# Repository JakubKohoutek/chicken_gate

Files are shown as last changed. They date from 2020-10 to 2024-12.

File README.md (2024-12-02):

# Chicken Gate

This repository contains circuit diagram and code for low power chicken door using
ESP-8266 (ESP-12) microcontroller, DS3231 RTC module and 28BYJ-48 stepper motor.

## Description

Purpose of this project is to create a chicken door that will automatically open in the
given time in the morning and close in the given time in the evening.

Besides this automatic procedures, manual operation is also allowed using external button
to open or close gate whenever needed.

Configuration and time setting is possible via long pressing the external button - that
will start a WiFi access point with captive portal, so once user connects to the
`chicken-gate` WiFi, he is redirected to the settings page, where it is possible to
synchronize time or set a different timer for opening/closing the gate.

## Circuit Diagram

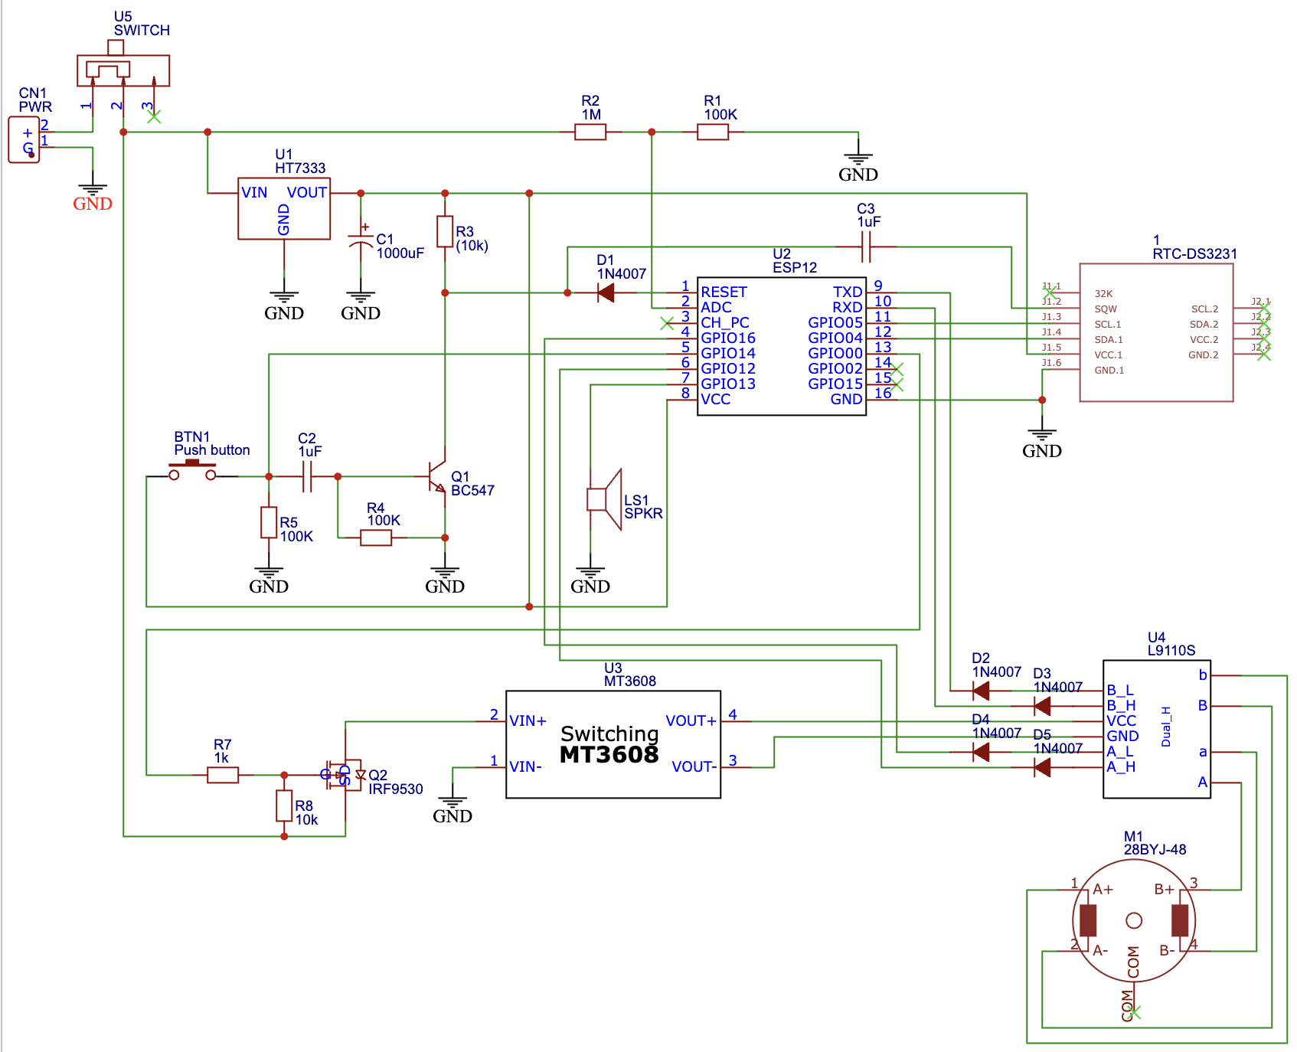
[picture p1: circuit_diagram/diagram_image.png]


## Compilation and Upload Configuration

* Board: Generic ESP8266 Module
* Upload speed: 115200
* Flash size: 4M (1M SPIFFS)

## Adjustments To Minimize Power Consumption

### RTC Module

DS3231 is a great real time clock chip, but the standard module drains too much power for
use in low power device running on battery. Fortunately it is possible to lower the power
consumption to just a few micro amps when making a few small adjustments described in
[this video](https://youtu.be/rG50U6bQhYo).

Namely, I made these adjustments:
- removed the 1k resistor to disable the power indicator LED
- bypassed the 200 ohm resistor from the "battery charging" circuit
- cut the trace from the + terminal of the battery to the VBAT pin of the chip
- added a 1N4148 diode from the + terminal of the battery to the VBAT pin of the chip
- added 1uF and 0.1uF decoupling capacitors between VBAT and GND
- lift up (or cut) the VCC pin of the DS3231 so that it doesn't connect to the board

This is how the board looks after the mods:

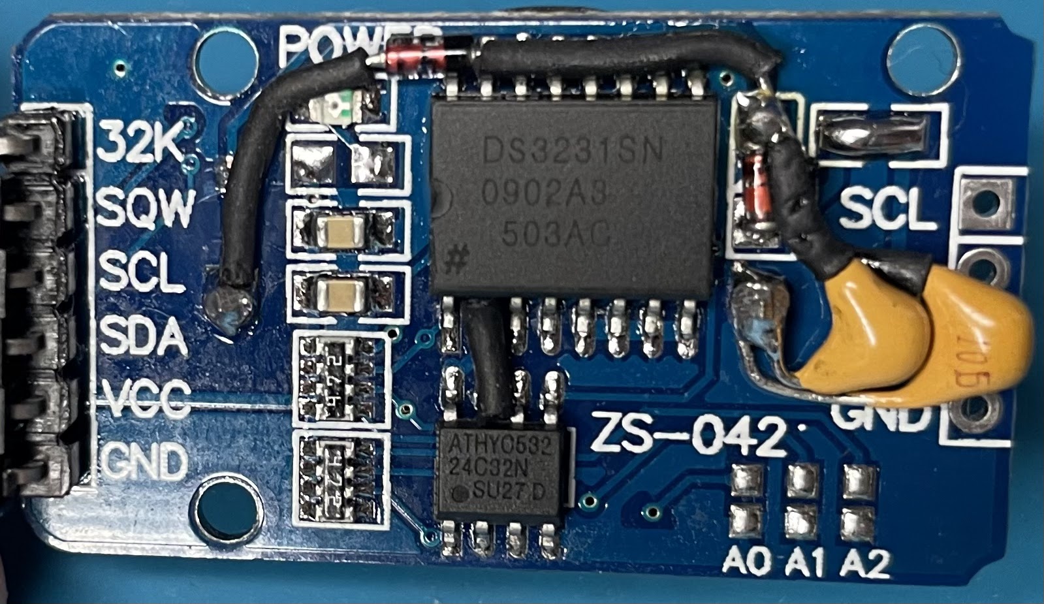
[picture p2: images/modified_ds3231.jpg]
Modified DS3231 board


Library I used to communicate with the module is available [here](https://github.com/Makuna/Rtc)

### ESP Microcontroller and Circuit

I was able to lower the power consumption of ESP-8266 board by using the deep sleep mode.
The board is woken up by an RTC module or by an external signal, so no circuit is in place
(GPIO16 connection to RST pin) for ESP to be able to wake up itself.

Current draw of the board and supplemental circuit in the deep sleep mode is about 27 uA
(~0.03 mA) and approximately 700 mA when opening/closing the gate (while stepper motor
is responsible for most of it). One operation cycle (closing, opening) takes in my case
34 seconds.

It means that in theory two operation cycles per day will drain 13.3 mAh while sleeping for
the rest of the day will drain additional 0.72 mAh. One standard day will therefore need
around 14 mAh.

It means that one 18650 battery with capacity of 1800 mAh should power the device for around
128 days, i.e. over 4 months.

## Adjustments To Improve Stepper Motor Torque

Standard 28BYJ-48 stepper motor is working in a unipolar mode. It is possible to increase
the motor torque using the bipolar mode, but it is necessary to adjust the motor in a way
described for instance in [this guide](http://www.jangeox.be/2013/10/change-unipolar-28byj-48-to-bipolar.html).

I followed these instructions and adjusted the stepper motor to increase its power to lift
up the gate.

## The Finished Product

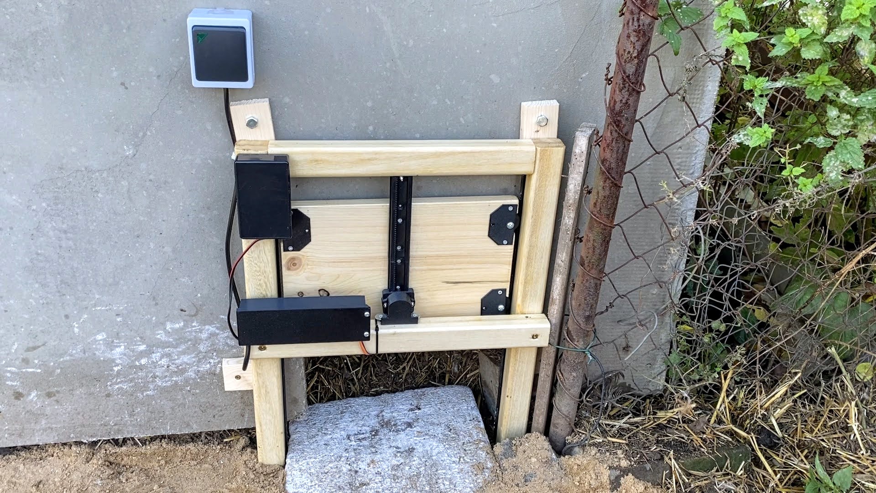
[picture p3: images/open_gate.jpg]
Open Gate

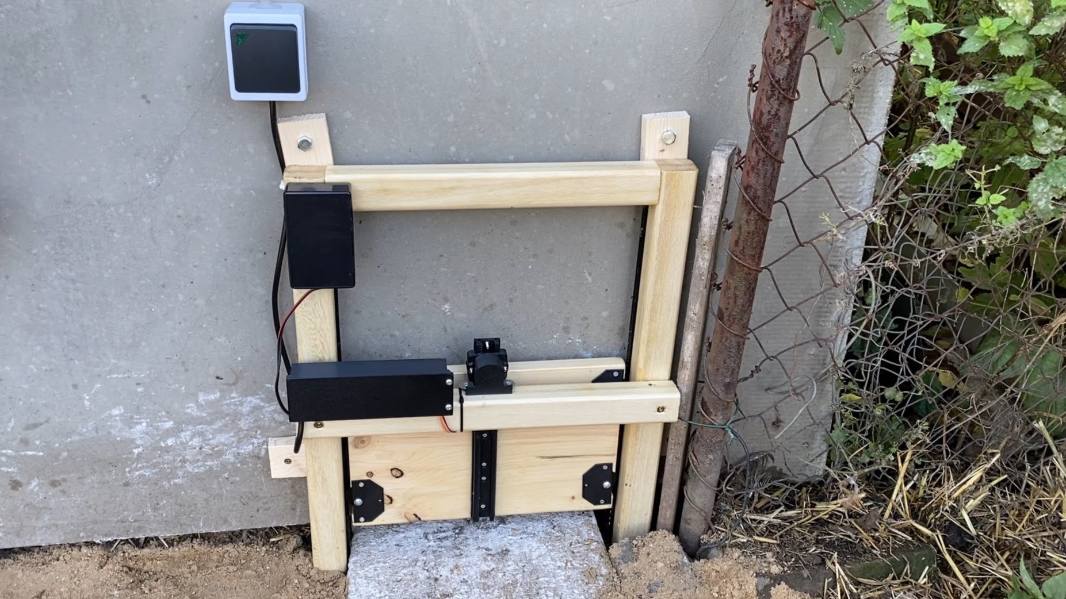
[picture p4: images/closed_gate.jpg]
Closed Gate

To see the video of working device, check out the [video on YouTube](https://youtu.be/cAucfu40Rm4).

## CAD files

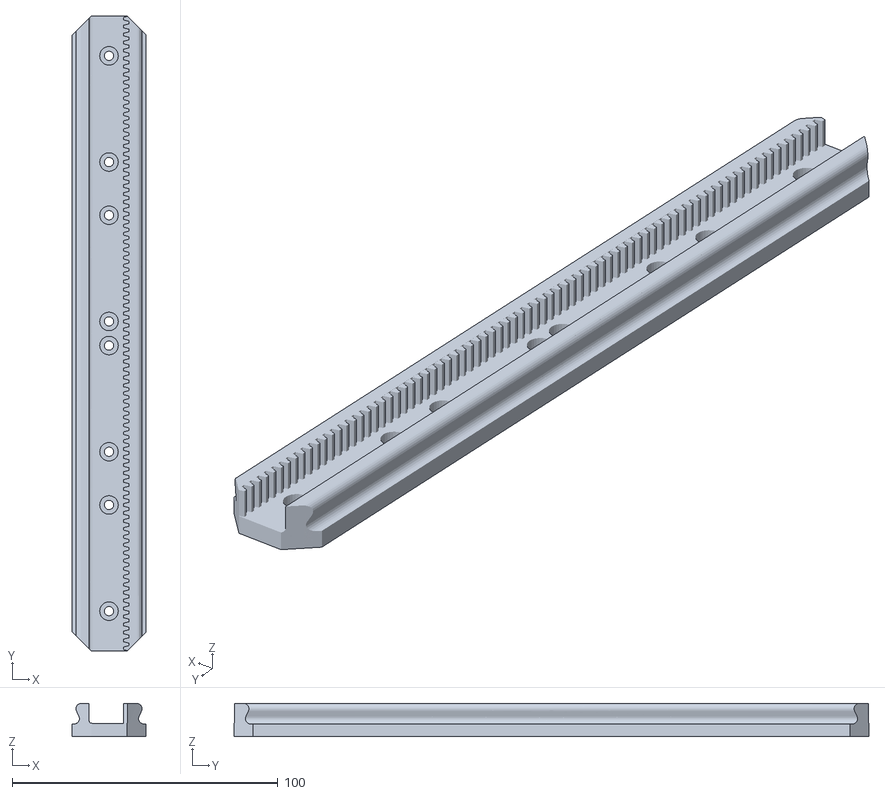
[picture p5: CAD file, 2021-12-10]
3D_models/slide.stl
28.0 x 239.1 x 12.5

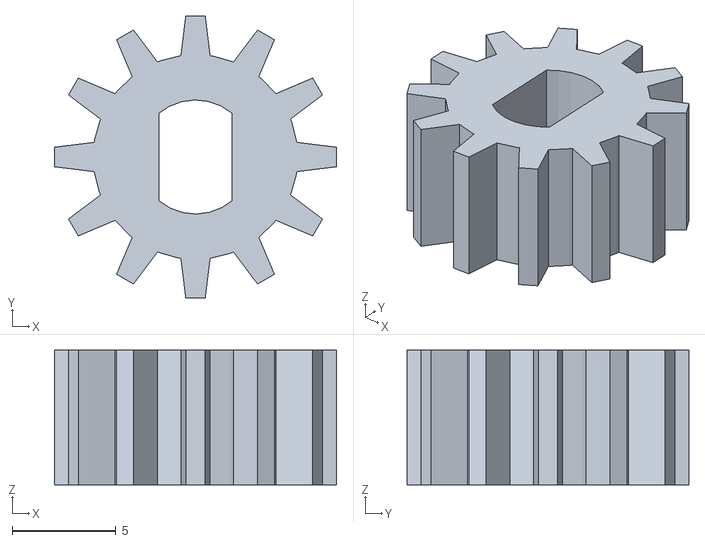
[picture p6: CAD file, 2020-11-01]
3D_models/motor_gear.stl
13.6 x 13.6 x 6.50

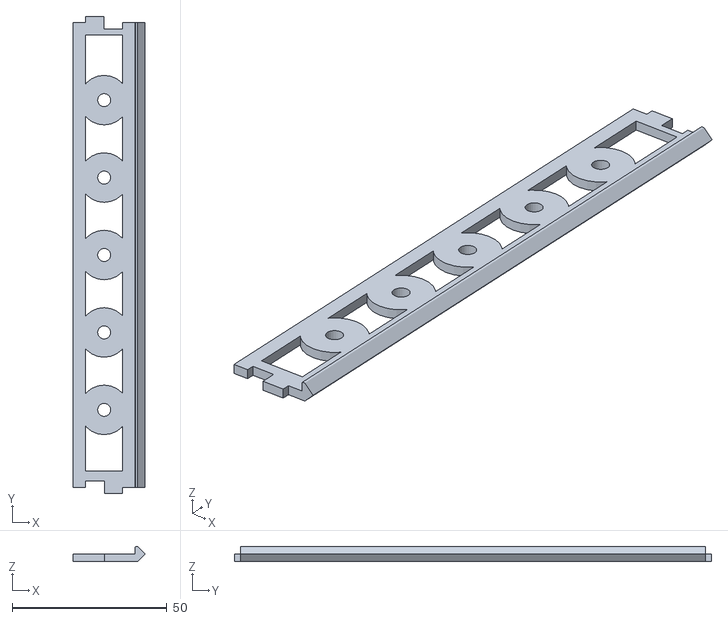
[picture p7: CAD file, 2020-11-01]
3D_models/stackable_rail_150mm.stl
23.1 x 154.0 x 4.80

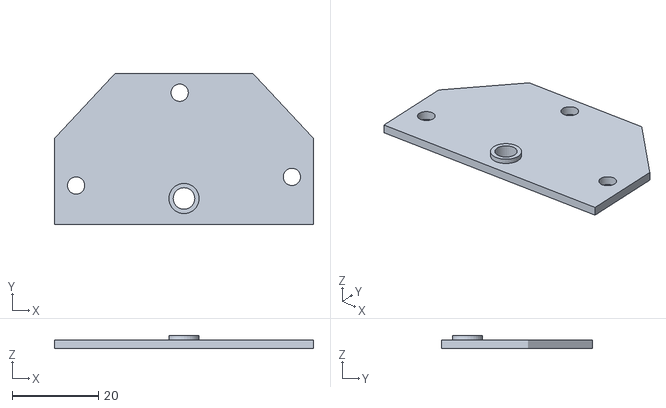
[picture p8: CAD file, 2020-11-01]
3D_models/wheel_holder_right.stl
60.0 x 34.9 x 3.10

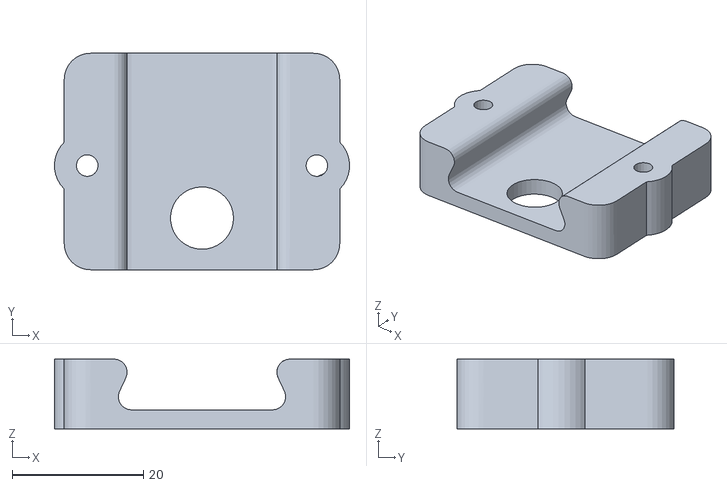
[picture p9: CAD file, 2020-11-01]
3D_models/motor_mount.stl
45.0 x 33.0 x 10.6

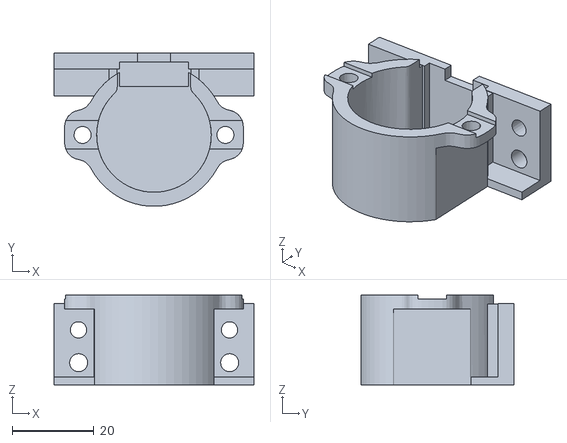
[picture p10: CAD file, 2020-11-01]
3D_models/28BYJ_housing.stl
49.0 x 37.6 x 22.0

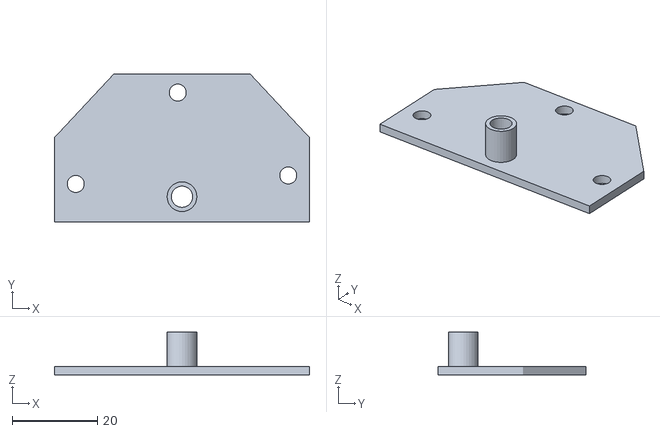
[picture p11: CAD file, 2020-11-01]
3D_models/wheel_holder_left.stl
60.0 x 34.9 x 10.1

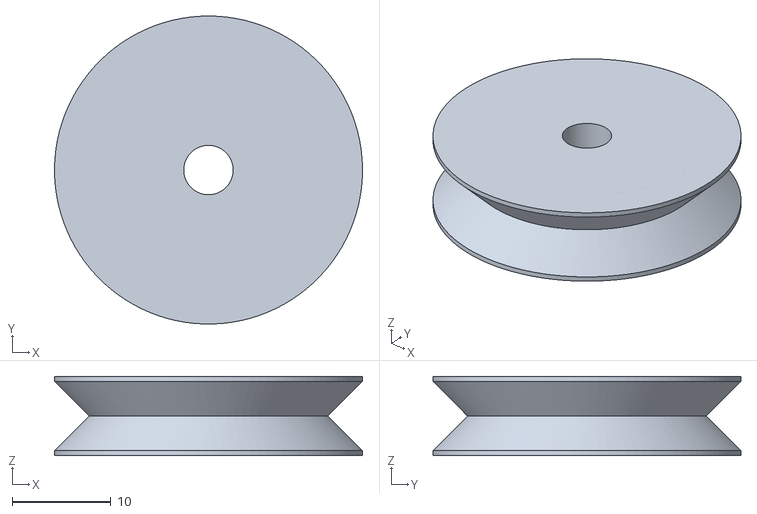
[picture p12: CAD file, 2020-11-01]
3D_models/wheel.stl
31.2 x 31.2 x 8.00

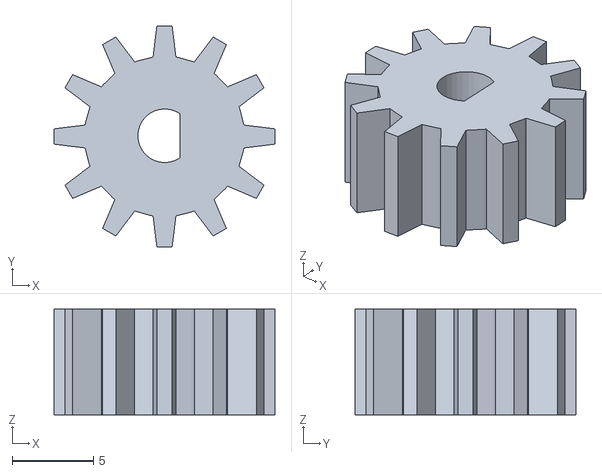
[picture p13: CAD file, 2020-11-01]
3D_models/gear_for_n20_motor.stl
13.6 x 13.6 x 6.50

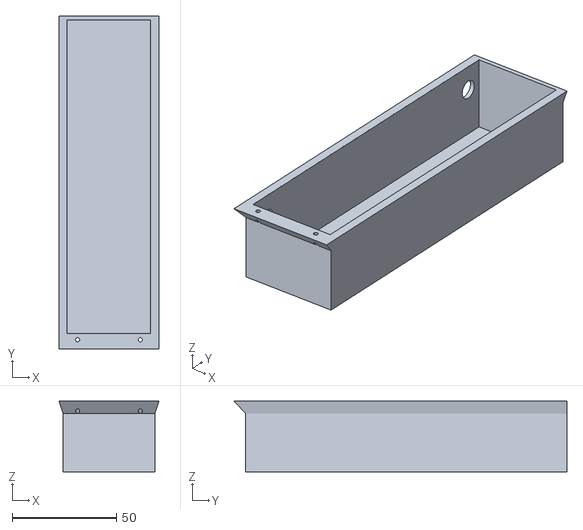
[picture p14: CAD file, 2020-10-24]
3D_models/electronics_housing_case.stl
48.0 x 159.5 x 34.0

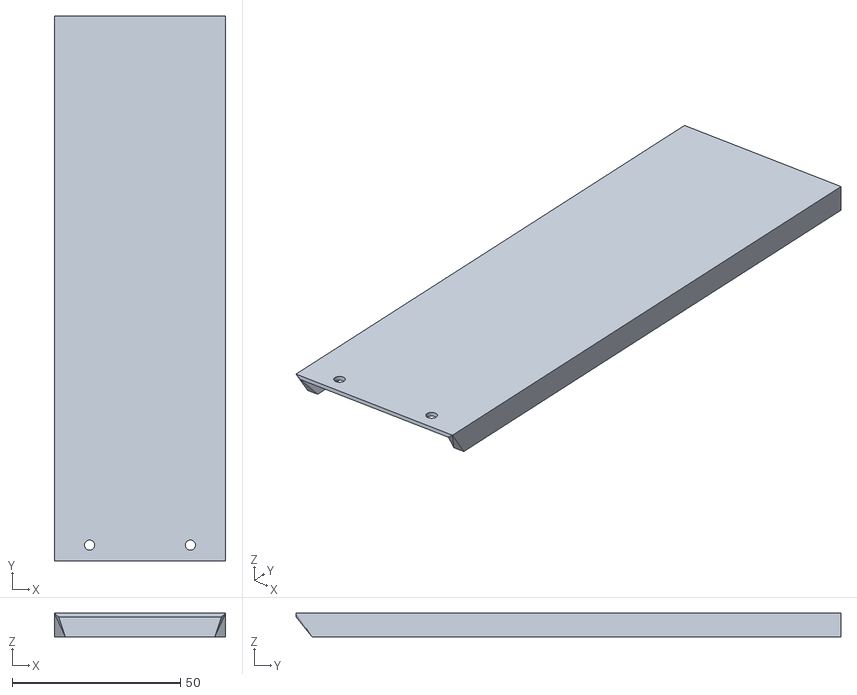
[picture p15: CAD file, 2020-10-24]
3D_models/electronics_housing_lid.stl
51.0 x 162.1 x 7.00

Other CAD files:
3D_models/28BYJ_housing.blend
3D_models/electronics_housing.blend
3D_models/gear_for_n20_motor.blend
3D_models/slide.blend
3D_models/wheel.blend
3D_models/wheel_holder_left.blend
3D_models/wheel_holder_right.blend

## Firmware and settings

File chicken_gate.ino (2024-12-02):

#include "config.h"
#include "melody.h"
#include "rtc.h"
#include "server.h"
#include "voltage.h"
#include "motor.h"
#include "memory.h"

#define LED_PIN          2
#define BUTTON_PIN       14

void setup () {
  pinMode(LED_PIN,    OUTPUT);
  pinMode(BUZZER_PIN, OUTPUT);
  pinMode(BUTTON_PIN, INPUT);

  digitalWrite(LED_PIN, LOW);

  initiateMemory();

  // NOTE: enabling serial will occupy TX (GPIO 1) and RX (GPIO 3) ports that can't be used then
  // Serial.begin(115200);

  // NOTE - RTC will occupy pin 0 once initiated, we must count with that
  initiateRtc();

  // Deal with the real time clock module alarms first
  DS3231AlarmFlag flag = Rtc.LatchAlarmsTriggeredFlags();

  if (flag & DS3231AlarmFlag_Alarm1) {
    openGate();
    sleep();
  }

  if (flag & DS3231AlarmFlag_Alarm2) {
    closeGate();
    sleep();
  }

  // Check if button is long pressed. If so, start the captive portal
  delay(500);
  if (digitalRead(BUTTON_PIN) == HIGH) {
    delay(1500);
    if (digitalRead(BUTTON_PIN) == HIGH) {
      playMelody(melodyBeep, melodyBeepLength);
      startServer();
      sleep();
    }
  }

  // If button is not long pressed, open or close the gate based on its state
  // writeToMemory(STATE_ADDRESS, OPEN); // Only run this once to initiate the memory
  unsigned long gateStatus = readFromMemory(STATE_ADDRESS);

  if (gateStatus == CLOSE) {
    openGate();
    sleep();
  }

  if (gateStatus == OPEN) {
    closeGate();
    sleep();
  }

  // We should never get here, but if something unexpected happens, go to sleep to save power
  sleep();
}

void sleep () {
  digitalWrite(LED_PIN, HIGH);
  ESP.deepSleep(0);
}

void loop () {
  // do nothing here
}

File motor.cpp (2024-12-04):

#include <Stepper.h>

#include "Arduino.h"
#include "motor.h"
#include "melody.h"
#include "memory.h"

// 2036 is one full turn. Must be divisible by 4 as the motor is 4 step
#define ONE_TURN    2036

// Max reliable speed: 10
#define SPEED       8

// Number of steps required to fully open or close gate
#define STEPS_COUNT 8800

Stepper stepper = Stepper(ONE_TURN, STEPPER_PIN_1, STEPPER_PIN_2, STEPPER_PIN_3, STEPPER_PIN_4);

void powerUpMotor () {
  pinMode(STEPPER_PIN_1, OUTPUT);
  pinMode(STEPPER_PIN_2, OUTPUT);
  pinMode(STEPPER_PIN_3, OUTPUT);
  pinMode(STEPPER_PIN_4, OUTPUT);
  pinMode(MOTOR_POWER_PIN, OUTPUT);
  digitalWrite(MOTOR_POWER_PIN, LOW);
  stepper.setSpeed(SPEED);
};

void powerDownMotor () {
  digitalWrite(MOTOR_POWER_PIN, HIGH);
  pinMode(STEPPER_PIN_1, INPUT);
  pinMode(STEPPER_PIN_2, INPUT);
  pinMode(STEPPER_PIN_3, INPUT);
  pinMode(STEPPER_PIN_4, INPUT);
}

void openGate () {
  if(readFromMemory(STATE_ADDRESS) == OPEN) {
    return;
  }
  playMelody(melodyUp, melodyUpLength);
  powerUpMotor();
  int count = 0;
  while (count < STEPS_COUNT) {
    stepper.step(-1);
    count++;
    // NOTE: we must use yield, otherwise ESP will restart after some time
    yield();
  }
  powerDownMotor();
  writeToMemory(STATE_ADDRESS, OPEN);
};

void closeGate () {
  if(readFromMemory(STATE_ADDRESS) == CLOSE) {
    return;
  }
  playMelody(melodyDown, melodyDownLength);
  powerUpMotor();
  int count = 0;
  while (count < STEPS_COUNT) {
    stepper.step(1);
    count++;
    // NOTE: we must use yield, otherwise ESP will restart after some time
    yield();
  }
  powerDownMotor();
  writeToMemory(STATE_ADDRESS, CLOSE);
};

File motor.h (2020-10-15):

#ifndef MOTOR_H
#define MOTOR_H

#define MOTOR_POWER_PIN       0
#define STEPPER_PIN_1         1
#define STEPPER_PIN_2         3
#define STEPPER_PIN_3         12
#define STEPPER_PIN_4         16

#define STATE_ADDRESS         0
#define CLOSE                 0
#define OPEN                  1

void powerUpMotor ();

void powerDownMotor ();

void openGate ();

void closeGate ();

#endif // MOTOR_H

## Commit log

2020-09-22 Add circuit diagram
2020-09-28 Show voltage in captive portal
2020-10-11 Add module controlling the stepper motor
2020-10-16 Clean up code, fix minor bugs, add server timeout
    [chicken_gate.ino, server.cpp]
2020-10-24 Add pictures of completed device
2020-10-24 Add 3D model for electorincs housing case
    [electronics_housing.blend, electronics_housing_case.stl, electronics_housing_lid.stl]
2020-11-01 Update circuit diagram
2020-11-01 Add models for 3D printed parts
    [28BYJ_housing.blend, 28BYJ_housing.stl, gear_for_n20_motor.blend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]
2021-12-10 Add modified geared slide
    Slide that is not stackable, but it has exactly the required length.
    [slide.blend, slide.stl]
2024-12-04 Improve the circuit
